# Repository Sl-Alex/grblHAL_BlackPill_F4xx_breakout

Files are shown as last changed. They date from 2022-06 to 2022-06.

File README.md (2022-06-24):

# What is it
It's a breakout board for F411 board (black pill) running [grblHAL FW][grblhal_fw]. It is compatible with the default black pill mapping.

## What is tested and confirmed to work

Limits, step/dir outputs and probing are tested and work fine.

> Limits and probing inputs (especially probing) enable a very convenient tool change procedure, when the only thing you have to do is to change the tool and click "cycle start".

Buttons, step enable and spindle enable also work, spindle PWM and auxiliary inputs/outputs are not tested. 

## Pinout

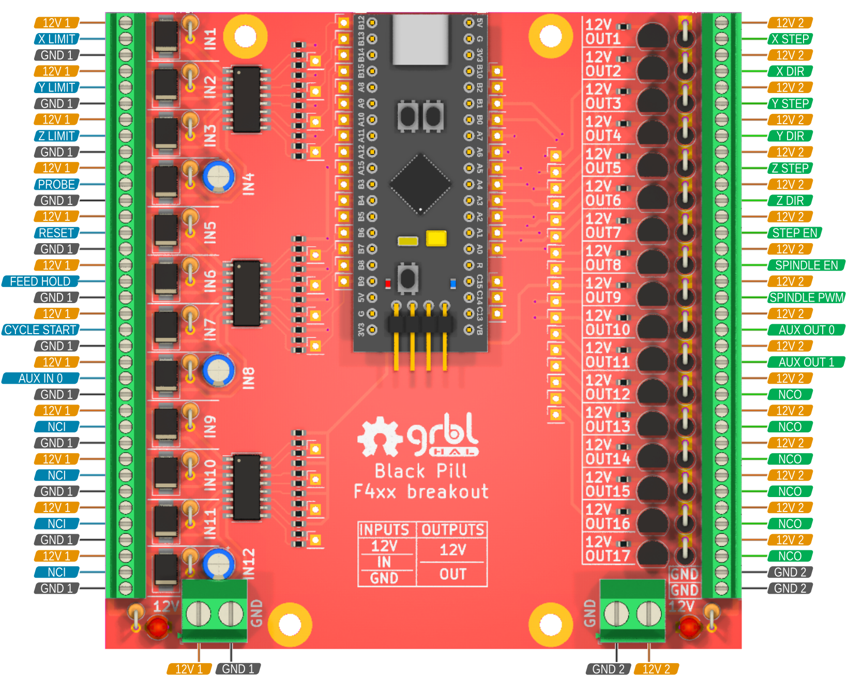
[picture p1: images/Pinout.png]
Pinout


The left part of the board is fully isolated from the right part, provided that two isolated power supplies are used.

There is no isolation between the MCU board and the outputs, but this is not a problem taking into account that all these outputs go either to optocouplers or relays.

```NCI``` stands for **N**on-**C**onnected **I**nput, ```NCO``` is an output.

## Remarks

All outputs provide 12V, so be careful connecting step motor drivers without any current limiting circuit.
Some drivers have just one resistor in series with the optocoupler LED, others have a bit more complex constant current circuits, like this:

![Constant current][constant_current]

Most of the drivers without the constant current circuit expect 5V input, so adding a resistor in series with the driver input would be a good solution.
As an alternative, 5V power supply could be used for the output part.

[grblhal_fw]: https://github.com/grblHAL
[pinout]: images/Pinout.png
[constant_current]: images/ConstantCurrent.png

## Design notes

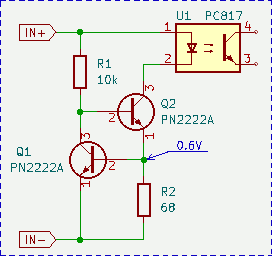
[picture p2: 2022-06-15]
images/ConstantCurrent.png

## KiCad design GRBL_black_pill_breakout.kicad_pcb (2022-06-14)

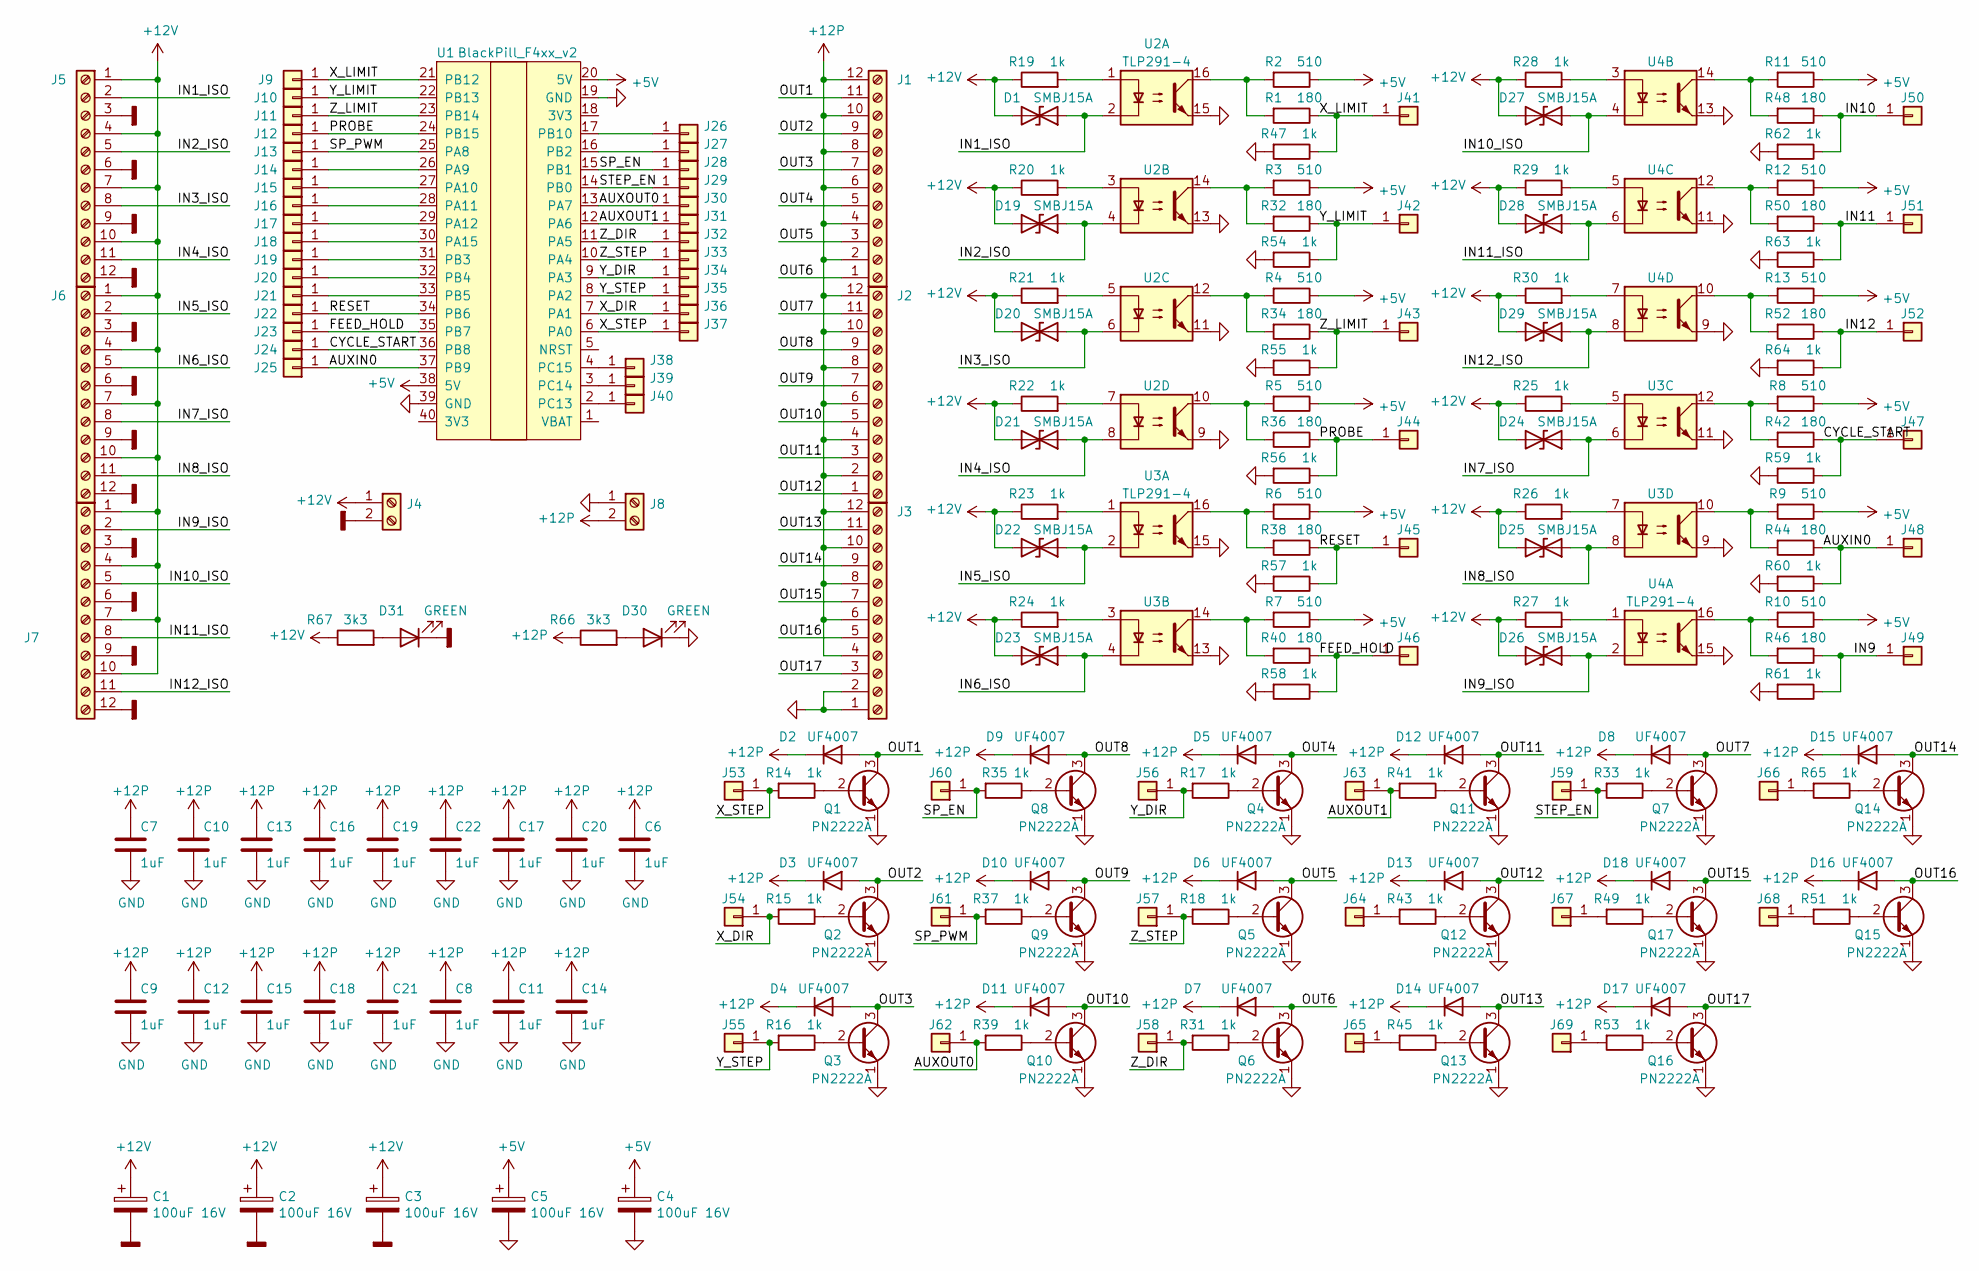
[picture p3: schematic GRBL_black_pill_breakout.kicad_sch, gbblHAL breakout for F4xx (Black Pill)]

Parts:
C1, C2, C3, C4, C5: 100uF 16V; CP_Radial_D5.0mm_P2.50mm
C6, C7, C8, C9, C10, C11, C12, C13, C14, C15, C16, C17, C18, C19, C20, C21, C22: 1uF; C_0603_1608Metric
D1, D19, D20, D21, D22, D23, D24, D25, D26, D27, D28, D29: SMBJ15A; D_SMB
D2, D3, D4, D5, D6, D7, D8, D9, D10, D11, D12, D13, D14, D15, D16, D17, D18: UF4007; D_DO-41_SOD81_P2.54mm_Vertical_KathodeUp
D30, D31: GREEN; LED_D3.0mm
J1, J2, J3, J5, J6, J7: Screw_Terminal_01x12; TerminalBlock_Phoenix_MPT-0,5-12-2.54_1x12_P2.54mm_Horizont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
J4, J8: Screw_Terminal_01x02; TerminalBlock_Phoenix_MKDS-1,5-2-5.08_1x02_P5.08mm_Horizont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
J9, J10, J11, J12, J13, J14, J15, J16, J17, J18, J19, J20, J21, J22, J23, J24, J25, J26, J27, J28, J29, J30, J31, J32, J33, J34, J35, J36, J37, J38, J39, J40, J41, J42, J43, J44, J45, J46, J47, J48, J49, J50, J51, J52, J53, J54, J55, J56, J57, J58, J59, J60, J61, J62, J63, J64, J65, J66, J67, J68, J69: Conn_01x01; PinHeader_1x01_P2.54mm_Vertical
Q1, Q2, Q3, Q4, Q5, Q6, Q7, Q8, Q9, Q10, Q11, Q12, Q13, Q14, Q15, Q16, Q17: PN2222A; TO-92_Inline
R1, R32, R34, R36, R38, R40, R42, R44, R46, R48, R50, R52: 180; R_0603_1608Metric
R2, R3, R4, R5, R6, R7, R8, R9, R10, R11, R12, R13: 510; R_0603_1608Metric
R14, R15, R16, R17, R18, R31, R33, R35, R37, R39, R41, R43, R45, R47, R49, R51, R53, R54, R55, R56, R57, R58, R59, R60, R61, R62, R63, R64, R65: 1k; R_0603_1608Metric
R19, R20, R21, R22, R23, R24, R25, R26, R27, R28, R29, R30: 1k; R_Axial_DIN0207_L6.3mm_D2.5mm_P2.54mm_Vertical
R66, R67: 3k3; R_Axial_DIN0207_L6.3mm_D2.5mm_P2.54mm_Vertical
U1: BlackPill_F4xx_v2
U2, U3, U4: TLP291-4; SOP-16_4.4x10.4mm_P1.27mm

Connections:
+5V: C4.1, C5.1, R2.1, R3.1, R4.1, R5.1, R6.1, R7.1, R8.1, R9.1, R10.1, R11.1, R12.1, R13.1, U1.20 (5V), U1.38 (5V)
+12P: C6.1, C7.1, C8.1, C9.1, C10.1, C11.1, C12.1, C13.1, C14.1, C15.1, C16.1, C17.1, C18.1, C19.1, C20.1, C21.1, C22.1, D2.1 (K), D3.1 (K), D4.1 (K), D5.1 (K), D6.1 (K), D7.1 (K), D8.1 (K), D9.1 (K), D10.1 (K), D11.1 (K), D12.1 (K), D13.1 (K), D14.1 (K), D15.1 (K), D16.1 (K), D17.1 (K), D18.1 (K), J1.2, J1.4, J1.6, J1.8, J1.10, J1.12, J2.2, J2.4, J2.6, J2.8, J2.10, J2.12, J3.4, J3.6, J3.8, J3.10, J3.12, J8.2, R66.1
+12V: C1.1, C2.1, C3.1, D1.2 (A2), D19.2 (A2), D20.2 (A2), D21.2 (A2), D22.2 (A2), D23.2 (A2), D24.2 (A2), D25.2 (A2), D26.2 (A2), D27.2 (A2), D28.2 (A2), D29.2 (A2), J4.1, J5.1, J5.4, J5.7, J5.10, J6.1, J6.4, J6.7, J6.10, J7.1, J7.4, J7.7, J7.10, R19.1, R20.1, R21.1, R22.1, R23.1, R24.1, R25.1, R26.1, R27.1, R28.1, R29.1, R30.1, R67.1
/AUXIN0: J25.1, J48.1, R44.1, R60.1, U1.37 (PB9)
/AUXOUT0: J30.1, J62.1, R39.2, U1.13 (PA7)
/AUXOUT1: J31.1, J63.1, R41.2, U1.12 (PA6)
/CYCLE_START: J24.1, J47.1, R42.1, R59.1, U1.36 (PB8)
/FEED_HOLD: J23.1, J46.1, R40.1, R58.1, U1.35 (PB7)
/IN1_ISO: D1.1 (A1), J5.2, U2.2
/IN2_ISO: D19.1 (A1), J5.5, U2.4
/IN3_ISO: D20.1 (A1), J5.8, U2.6
/IN4_ISO: D21.1 (A1), J5.11, U2.8
/IN5_ISO: D22.1 (A1), J6.2, U3.2
/IN6_ISO: D23.1 (A1), J6.5, U3.4
/IN7_ISO: D24.1 (A1), J6.8, U3.6
/IN8_ISO: D25.1 (A1), J6.11, U3.8
/IN9: J49.1, R46.1, R61.1
/IN9_ISO: D26.1 (A1), J7.2, U4.2
/IN10: J50.1, R48.1, R62.1
/IN10_ISO: D27.1 (A1), J7.5, U4.4
/IN11: J51.1, R50.1, R63.1
/IN11_ISO: D28.1 (A1), J7.8, U4.6
/IN12: J52.1, R52.1, R64.1
/IN12_ISO: D29.1 (A1), J7.11, U4.8
/OUT1: D2.2 (A), J1.11, Q1.3 (C)
/OUT2: D3.2 (A), J1.9, Q2.3 (C)
/OUT3: D4.2 (A), J1.7, Q3.3 (C)
/OUT4: D5.2 (A), J1.5, Q4.3 (C)
/OUT5: D6.2 (A), J1.3, Q5.3 (C)
/OUT6: D7.2 (A), J1.1, Q6.3 (C)
/OUT7: D8.2 (A), J2.11, Q7.3 (C)
/OUT8: D9.2 (A), J2.9, Q8.3 (C)
/OUT9: D10.2 (A), J2.7, Q9.3 (C)
/OUT10: D11.2 (A), J2.5, Q10.3 (C)
/OUT11: D12.2 (A), J2.3, Q11.3 (C)
/OUT12: D13.2 (A), J2.1, Q12.3 (C)
/OUT13: D14.2 (A), J3.11, Q13.3 (C)
/OUT14: D15.2 (A), J3.9, Q14.3 (C)
/OUT15: D18.2 (A), J3.7, Q17.3 (C)
/OUT16: D16.2 (A), J3.5, Q15.3 (C)
/OUT17: D17.2 (A), J3.3, Q16.3 (C)
/PROBE: J12.1, J44.1, R36.1, R56.1, U1.24 (PB15)
/RESET: J22.1, J45.1, R38.1, R57.1, U1.34 (PB6)
/SP_EN: J28.1, J60.1, R35.2, U1.15 (PB1)
/SP_PWM: J13.1, J61.1, R37.2, U1.25 (PA8)
/STEP_EN: J29.1, J59.1, R33.2, U1.14 (PB0)
/X_DIR: J36.1, J54.1, R15.2, U1.7 (PA1)
/X_LIMIT: J9.1, J41.1, R1.1, R47.1, U1.21 (PB12)
/X_STEP: J37.1, J53.1, R14.2, U1.6 (PA0)
/Y_DIR: J34.1, J56.1, R17.2, U1.9 (PA3)
/Y_LIMIT: J10.1, J42.1, R32.1, R54.1, U1.22 (PB13)
/Y_STEP: J35.1, J55.1, R16.2, U1.8 (PA2)
/Z_DIR: J32.1, J58.1, R31.2, U1.11 (PA5)
/Z_LIMIT: J11.1, J43.1, R34.1, R55.1, U1.23 (PB14)
/Z_STEP: J33.1, J57.1, R18.2, U1.10 (PA4)
GND: C4.2, C5.2, C6.2, C7.2, C8.2, C9.2, C10.2, C11.2, C12.2, C13.2, C14.2, C15.2, C16.2, C17.2, C18.2, C19.2, C20.2, C21.2, C22.2, D30.1 (K), J3.1, J3.2, J8.1, Q1.1 (E), Q2.1 (E), Q3.1 (E), Q4.1 (E), Q5.1 (E), Q6.1 (E), Q7.1 (E), Q8.1 (E), Q9.1 (E), Q10.1 (E), Q11.1 (E), Q12.1 (E), Q13.1 (E), Q14.1 (E), Q15.1 (E), Q16.1 (E), Q17.1 (E), R47.2, R54.2, R55.2, R56.2, R57.2, R58.2, R59.2, R60.2, R61.2, R62.2, R63.2, R64.2, U1.19 (GND), U1.39 (GND), U2.9, U2.11, U2.13, U2.15, U3.9, U3.11, U3.13, U3.15, U4.9, U4.11, U4.13, U4.15
GNDD: C1.2, C2.2, C3.2, D31.1 (K), J4.2, J5.3, J5.6, J5.9, J5.12, J6.3, J6.6, J6.9, J6.12, J7.3, J7.6, J7.9, J7.12
unnamed: D30.2 (A), R66.2
unnamed: D31.2 (A), R67.2
unnamed: J14.1, U1.26 (PA9)
unnamed: J15.1, U1.27 (PA10)
unnamed: J16.1, U1.28 (PA11)
unnamed: J17.1, U1.29 (PA12)
unnamed: J18.1, U1.30 (PA15)
unnamed: J19.1, U1.31 (PB3)
unnamed: J20.1, U1.32 (PB4)
unnamed: J21.1, U1.33 (PB5)
unnamed: J26.1, U1.17 (PB10)
unnamed: J27.1, U1.16 (PB2)
unnamed: J38.1, U1.4 (PC15)
unnamed: J39.1, U1.3 (PC14)
unnamed: J40.1, U1.2 (PC13)
unnamed: J64.1, R43.2
unnamed: J65.1, R45.2
unnamed: J66.1, R65.2
unnamed: J67.1, R49.2
unnamed: J68.1, R51.2
unnamed: J69.1, R53.2
unnamed: Q1.2 (B), R14.1
unnamed: Q2.2 (B), R15.1
unnamed: Q3.2 (B), R16.1
unnamed: Q4.2 (B), R17.1
unnamed: Q5.2 (B), R18.1
unnamed: Q6.2 (B), R31.1
unnamed: Q7.2 (B), R33.1
unnamed: Q8.2 (B), R35.1
unnamed: Q9.2 (B), R37.1
unnamed: Q10.2 (B), R39.1
unnamed: Q11.2 (B), R41.1
unnamed: Q12.2 (B), R43.1
unnamed: Q13.2 (B), R45.1
unnamed: Q14.2 (B), R65.1
unnamed: Q15.2 (B), R51.1
unnamed: Q16.2 (B), R53.1
unnamed: Q17.2 (B), R49.1
unnamed: R1.2, R2.2, U2.16
unnamed: R3.2, R32.2, U2.14
unnamed: R10.2, R46.2, U4.16
unnamed: R11.2, R48.2, U4.14
unnamed: R12.2, R50.2, U4.12
unnamed: R13.2, R52.2, U4.10
unnamed: R19.2, U2.1
unnamed: R20.2, U2.3
unnamed: R21.2, U2.5
unnamed: R22.2, U2.7
unnamed: R23.2, U3.1
unnamed: R24.2, U3.3
unnamed: R25.2, U3.5
unnamed: R26.2, U3.7
unnamed: R27.2, U4.1
unnamed: R28.2, U4.3
unnamed: R29.2, U4.5
unnamed: R30.2, U4.7
unnamed: R4.2, R34.2, U2.12
unnamed: R5.2, R36.2, U2.10
unnamed: R6.2, R38.2, U3.16
unnamed: R7.2, R40.2, U3.14
unnamed: R8.2, R42.2, U3.12
unnamed: R9.2, R44.2, U3.10

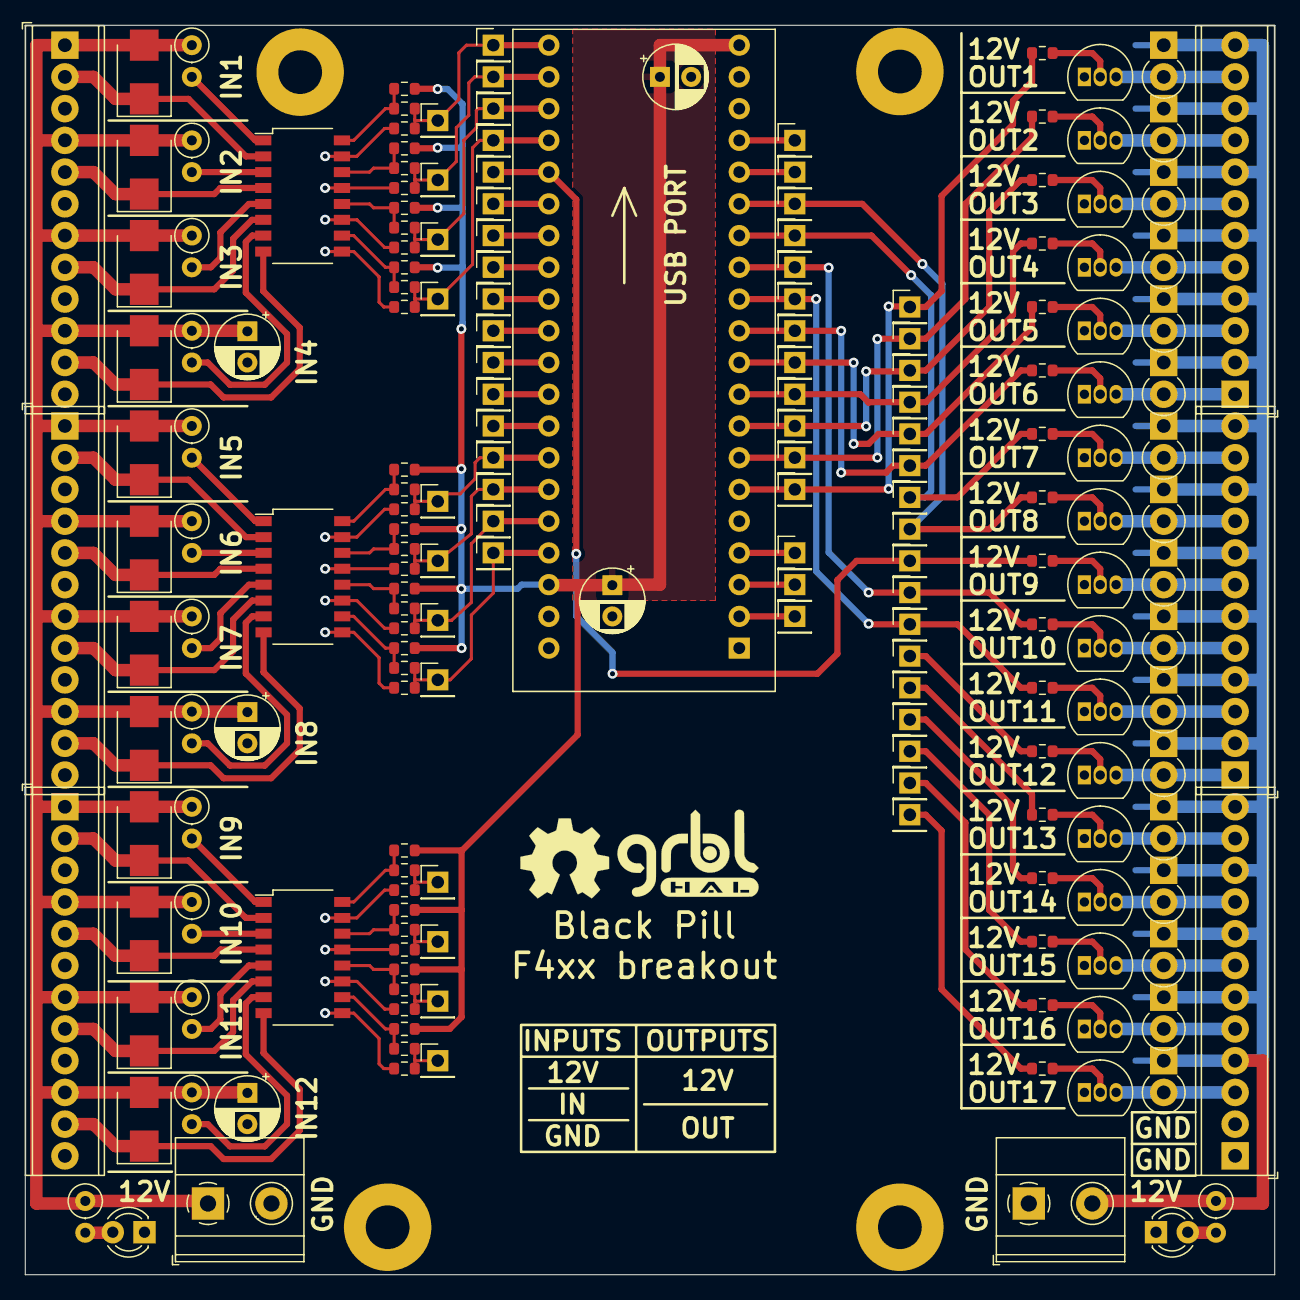
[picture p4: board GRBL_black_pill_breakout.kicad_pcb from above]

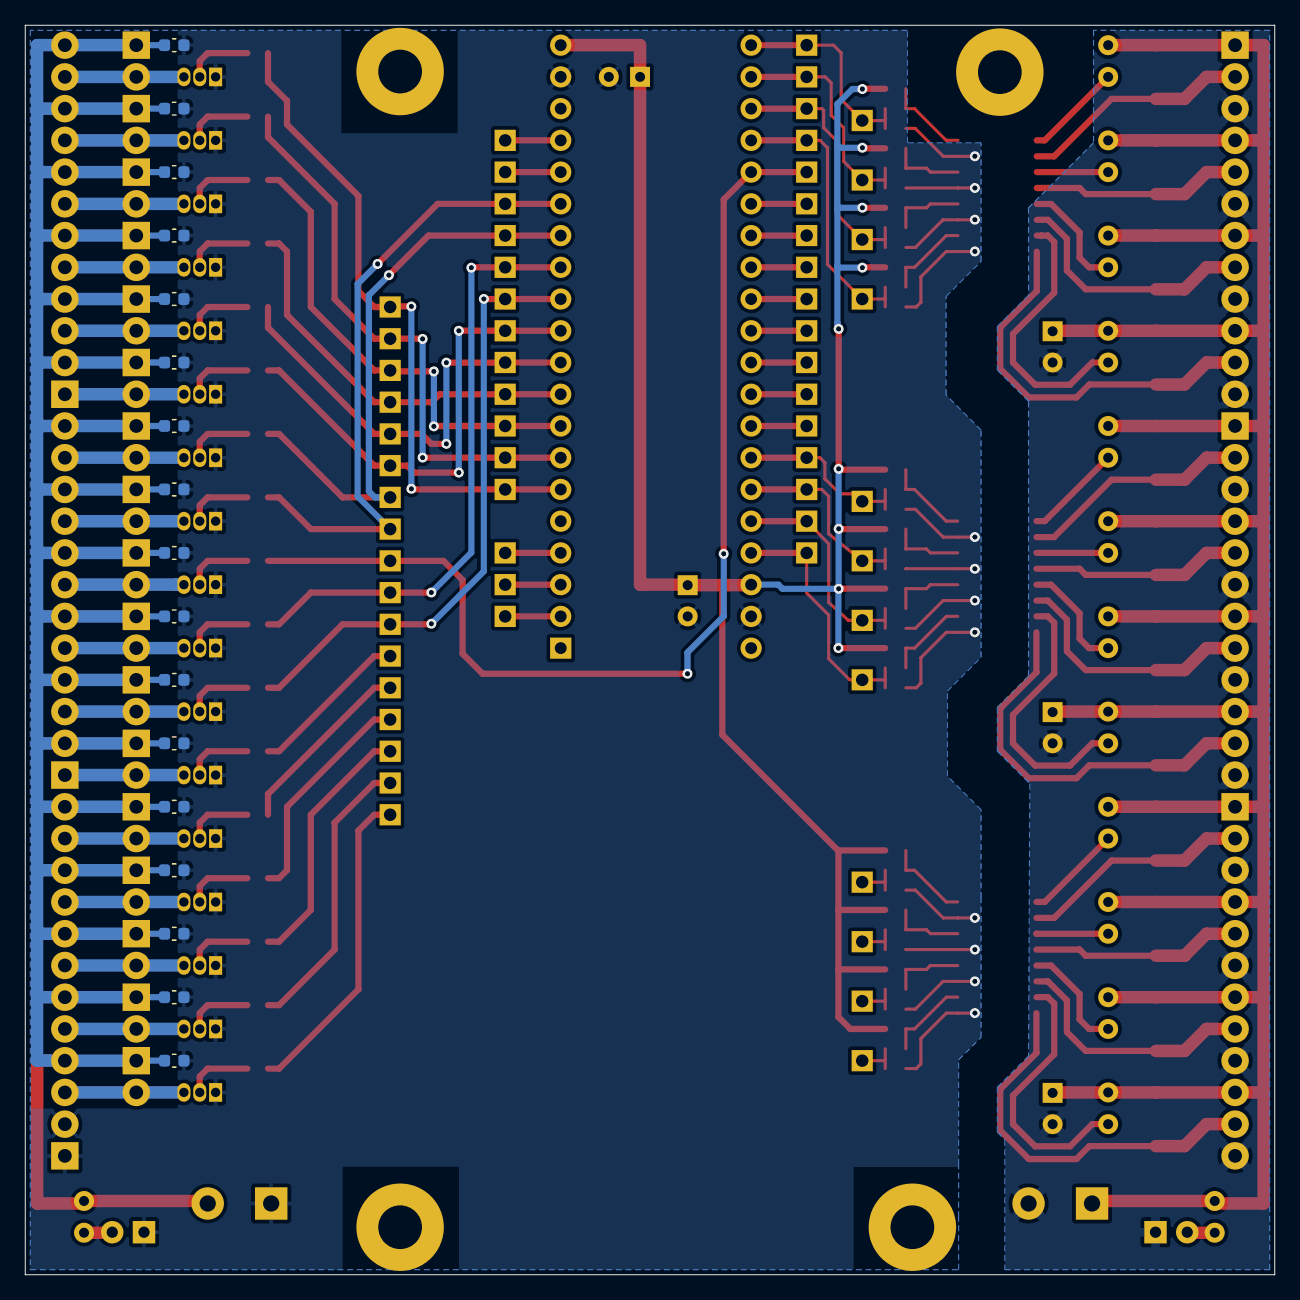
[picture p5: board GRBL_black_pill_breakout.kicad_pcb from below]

Board: 2 copper layers, 100.0 x 100.0 mm, 210 parts (17 on the bottom side), 119 nets.

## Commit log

2021-04-17 First prototype
    [GRBL_black_pill_breakout.kicad_pcb, GRBL_black_pill_breakout.sch]
2021-04-21 Flip 12V connectors, update values
    [GRBL_black_pill_breakout.kicad_pcb, GRBL_black_pill_breakout.sch]
2022-06-14 Update the board according to the official GrblHAL pinout for black pill
    [GRBL_black_pill_breakout.kicad_pcb, GRBL_black_pill_breakout.kicad_sch, GRBL_black_pill_breakout.sch]
